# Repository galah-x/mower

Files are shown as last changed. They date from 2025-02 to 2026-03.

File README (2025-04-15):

Repository for files to upgrade a Ryobi RM480e ride on battery mower
from its original 4 75AH lead acid batteries
to Lithium Iron Phosphate (LFP) 100AH batteries
With a battery balance facility.

The 12V LFP batteries have internal battery balance, to balance the 4 cells each contains.
This repo is about balancing the 4 12V batteries to each other.

Discussion at https://hackaday.io/project/202788-ryobi-480e-mower-lfp-battery-upgrade-with-balance

Repo signifiant contents:

VMON is the per battery voltage monitor and balance board
vmon/vmn/vmn.ino    arduino code for an esp32
vmon/vmon/vmon.pdf  board schematic
vmon/vmon/gerbers/  board manufacturing info
vmon/vmon           kicad layout directory

IMON is the current monitor from a current shunt
imon/imon.ino       arduino code for an esp32
vmon/imon/imon.pdf  schematic
there is no imon layout, its hacked onto a vmon board as I discovered a design oversight in the
adc on the mco board near the runup phase. Too much of a hurry to mow the lawn to wait for a pcb to be made and shipped.

MCO is the Mower comms controller board. This is where the mower logic runs.
mcomms/mco/mco.ino     and other files in that directory is the arduino source for the mco board
mcomms/mcomms.pdf      board schematic
mcomms/mcomms          kicad layout files
mcomms/mcomms/gerbers  pcb manufacturing files

MMC is the mower charge controller. Really its a display board next to the power supply with a LCD and
rotary encoder. It displays each battery voltage and balance state, charger voltage, charge current, charge state, mower temperature.
mcharger_if/mcharge_if.pdf       schematic
mcharger_if/mcc/mcc.ino          arduino code, together with remainder of the directory
mcharger_if/mcharger_if/         kicad layout dir
mcharger_if/mcharger_if/gerbers  pcb manufacturing information

PSU is a wifi to serial converter used to allow mco to control and monitor the replacement charger, made from a 1200W 60V smps module and a DPM8624 remote programmable power supply.
vichyctl/psu/psu.ino        arduino code for psu
vichyctl/vichyctl.pdf       schematic for board
vichyctl/vichyctl/gerbers/  layout files
vichyctl/vichyctl           kicad layout directory.   Originally a board to permit remote Wifi access to a vichy VC8145 multimeter 

I didn't draw a charger schematic.
Connect the mains to the smps power supply.
Connect the 60V out of the SMPS to the input pins of the DPM8624
Connect the 4 pins on the PSU board (5V, 0V, TX, RX) to the matching 4 control pins on the DPM86224.
Connect the 2 output pins on the DPM8624 to a charger cable likely repurposed from your old charger
in the charger plug, add a wire to connect the middle sense pin to +48V, ie charger positive. 

mower_system_connect is a top level schematic of new stuff in the mower.
mower_system_connect/mower_system_connect.pdf

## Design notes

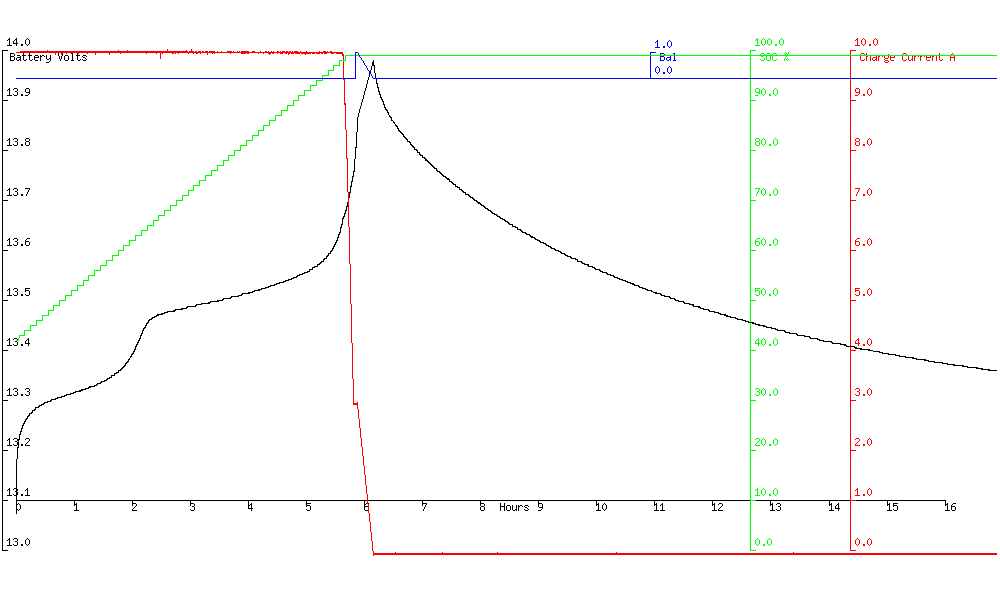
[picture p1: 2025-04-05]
graphs/run2_v.png

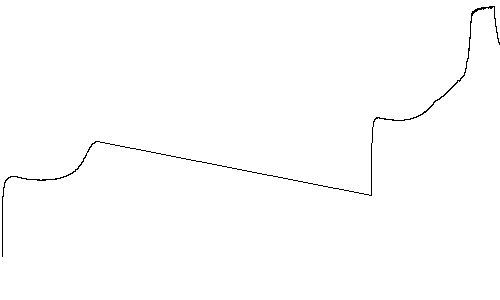
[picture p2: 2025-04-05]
graphs/run1_v.png

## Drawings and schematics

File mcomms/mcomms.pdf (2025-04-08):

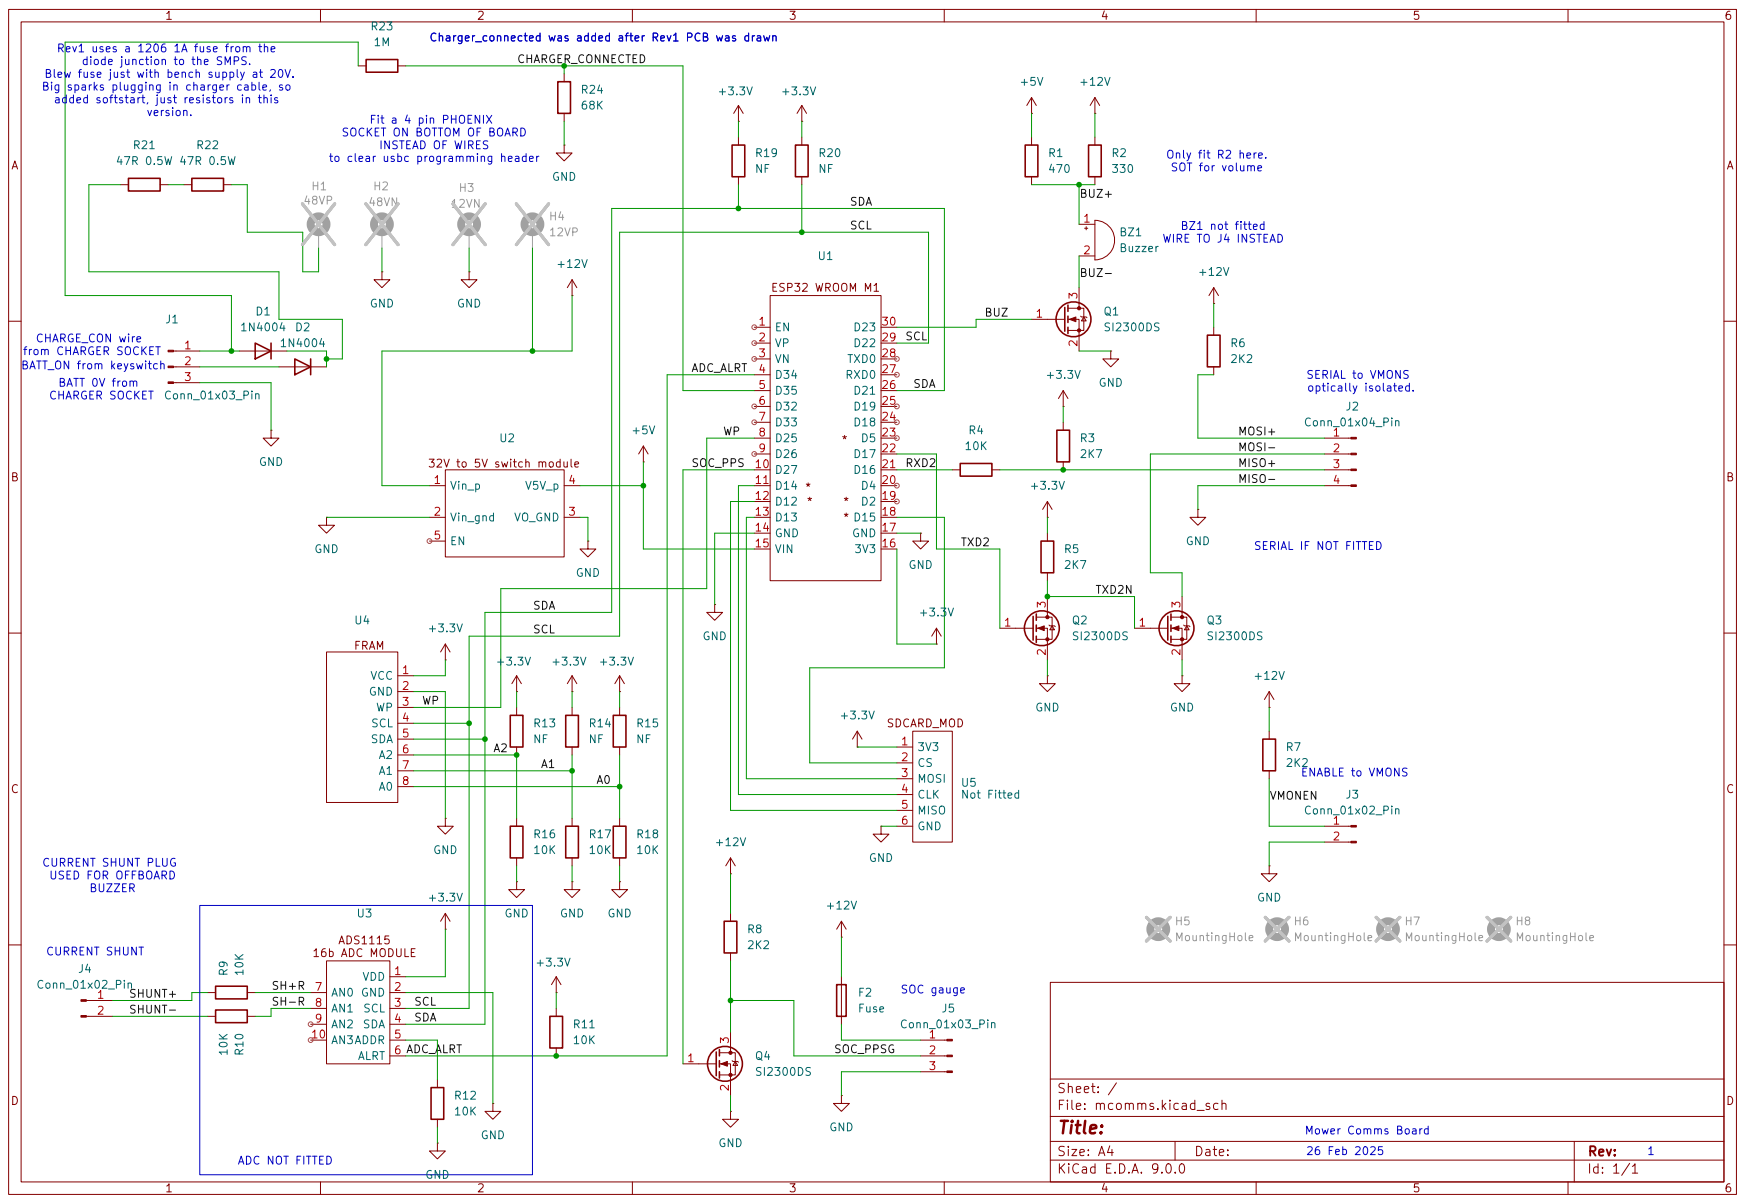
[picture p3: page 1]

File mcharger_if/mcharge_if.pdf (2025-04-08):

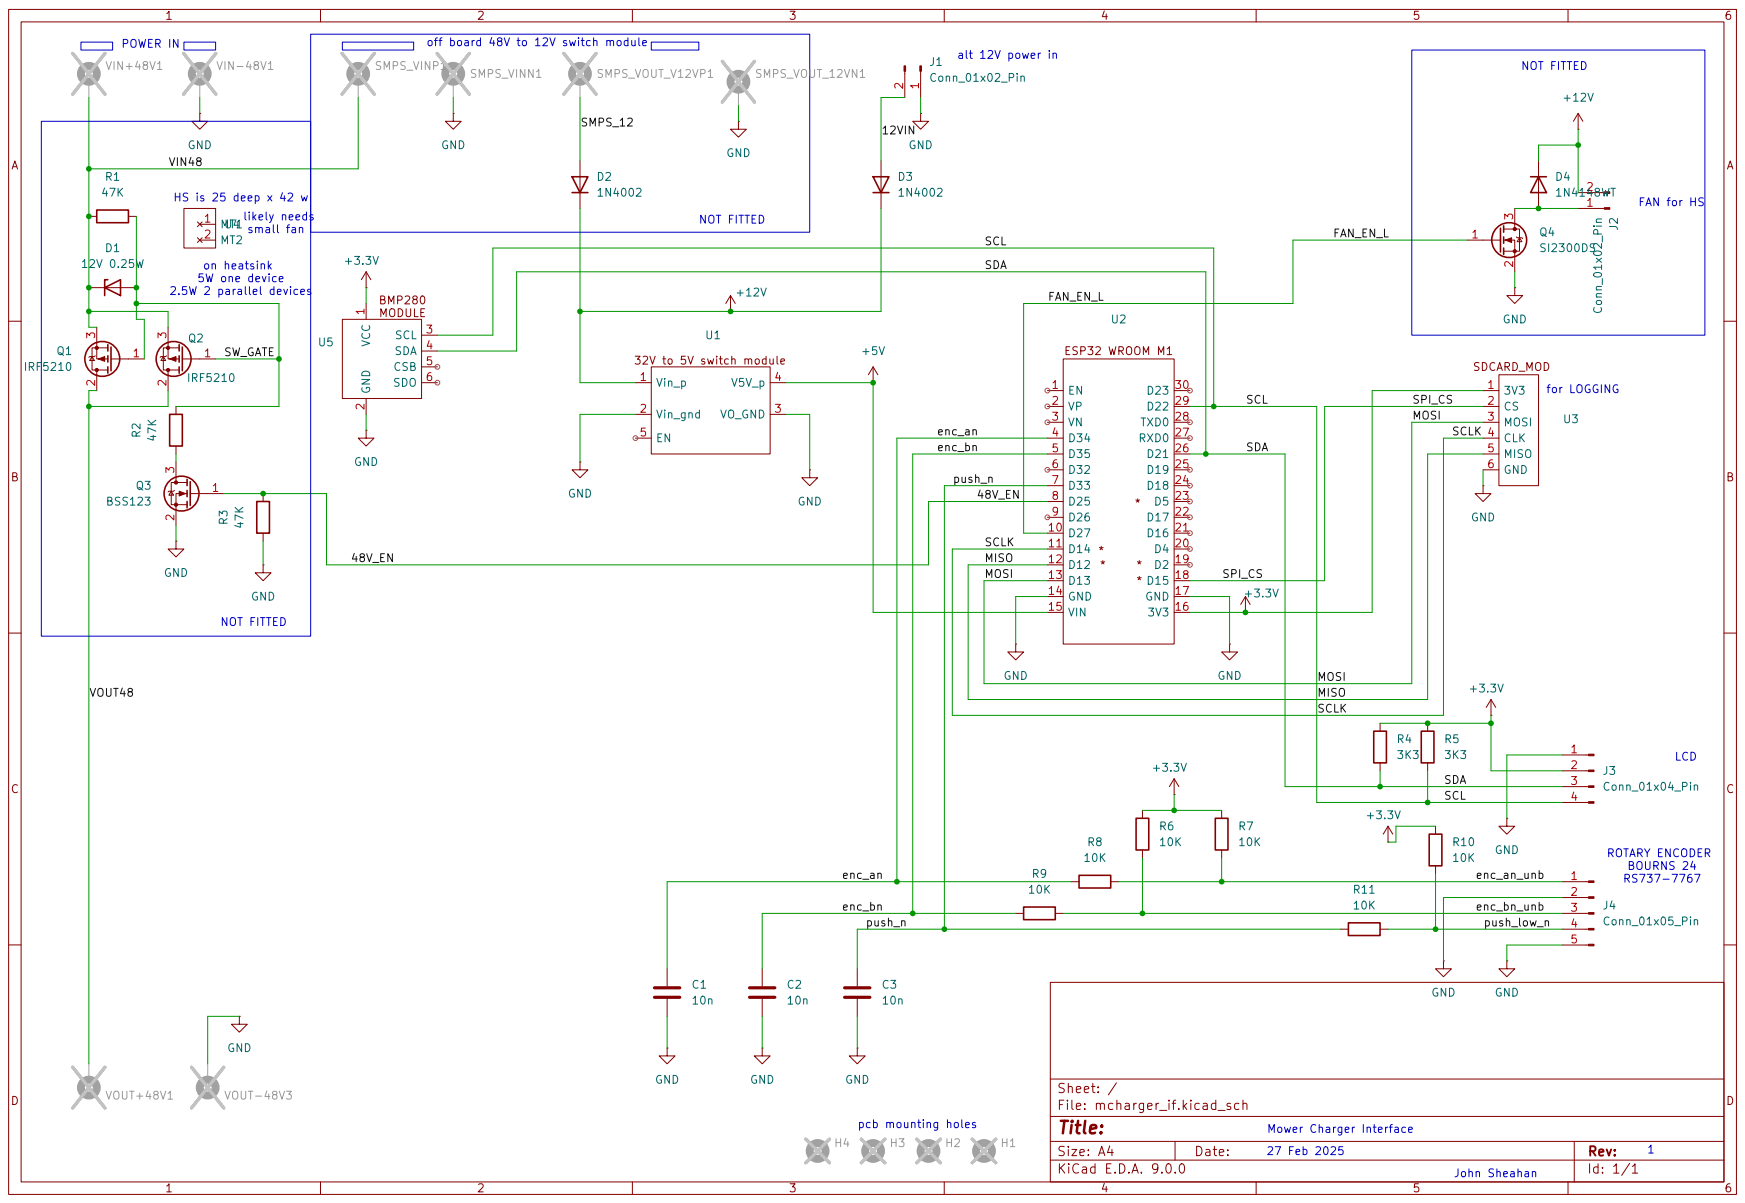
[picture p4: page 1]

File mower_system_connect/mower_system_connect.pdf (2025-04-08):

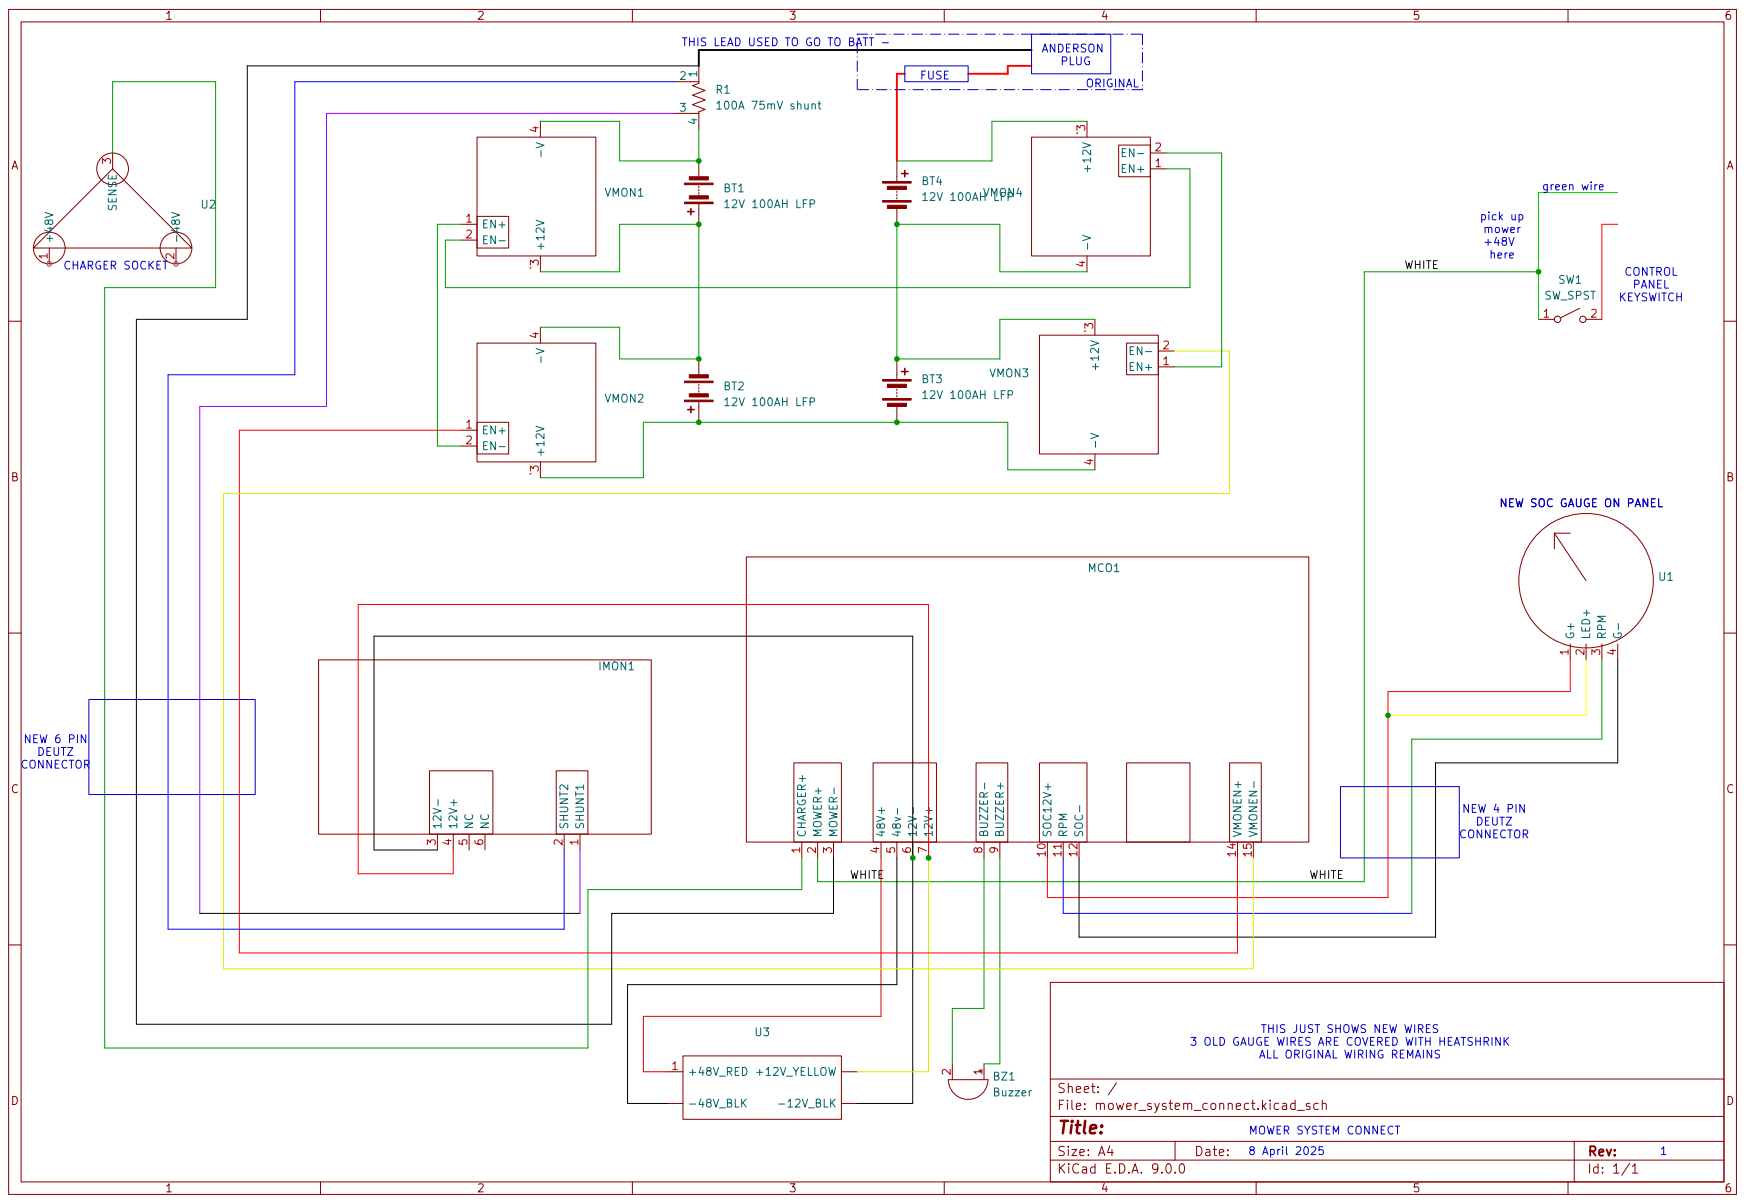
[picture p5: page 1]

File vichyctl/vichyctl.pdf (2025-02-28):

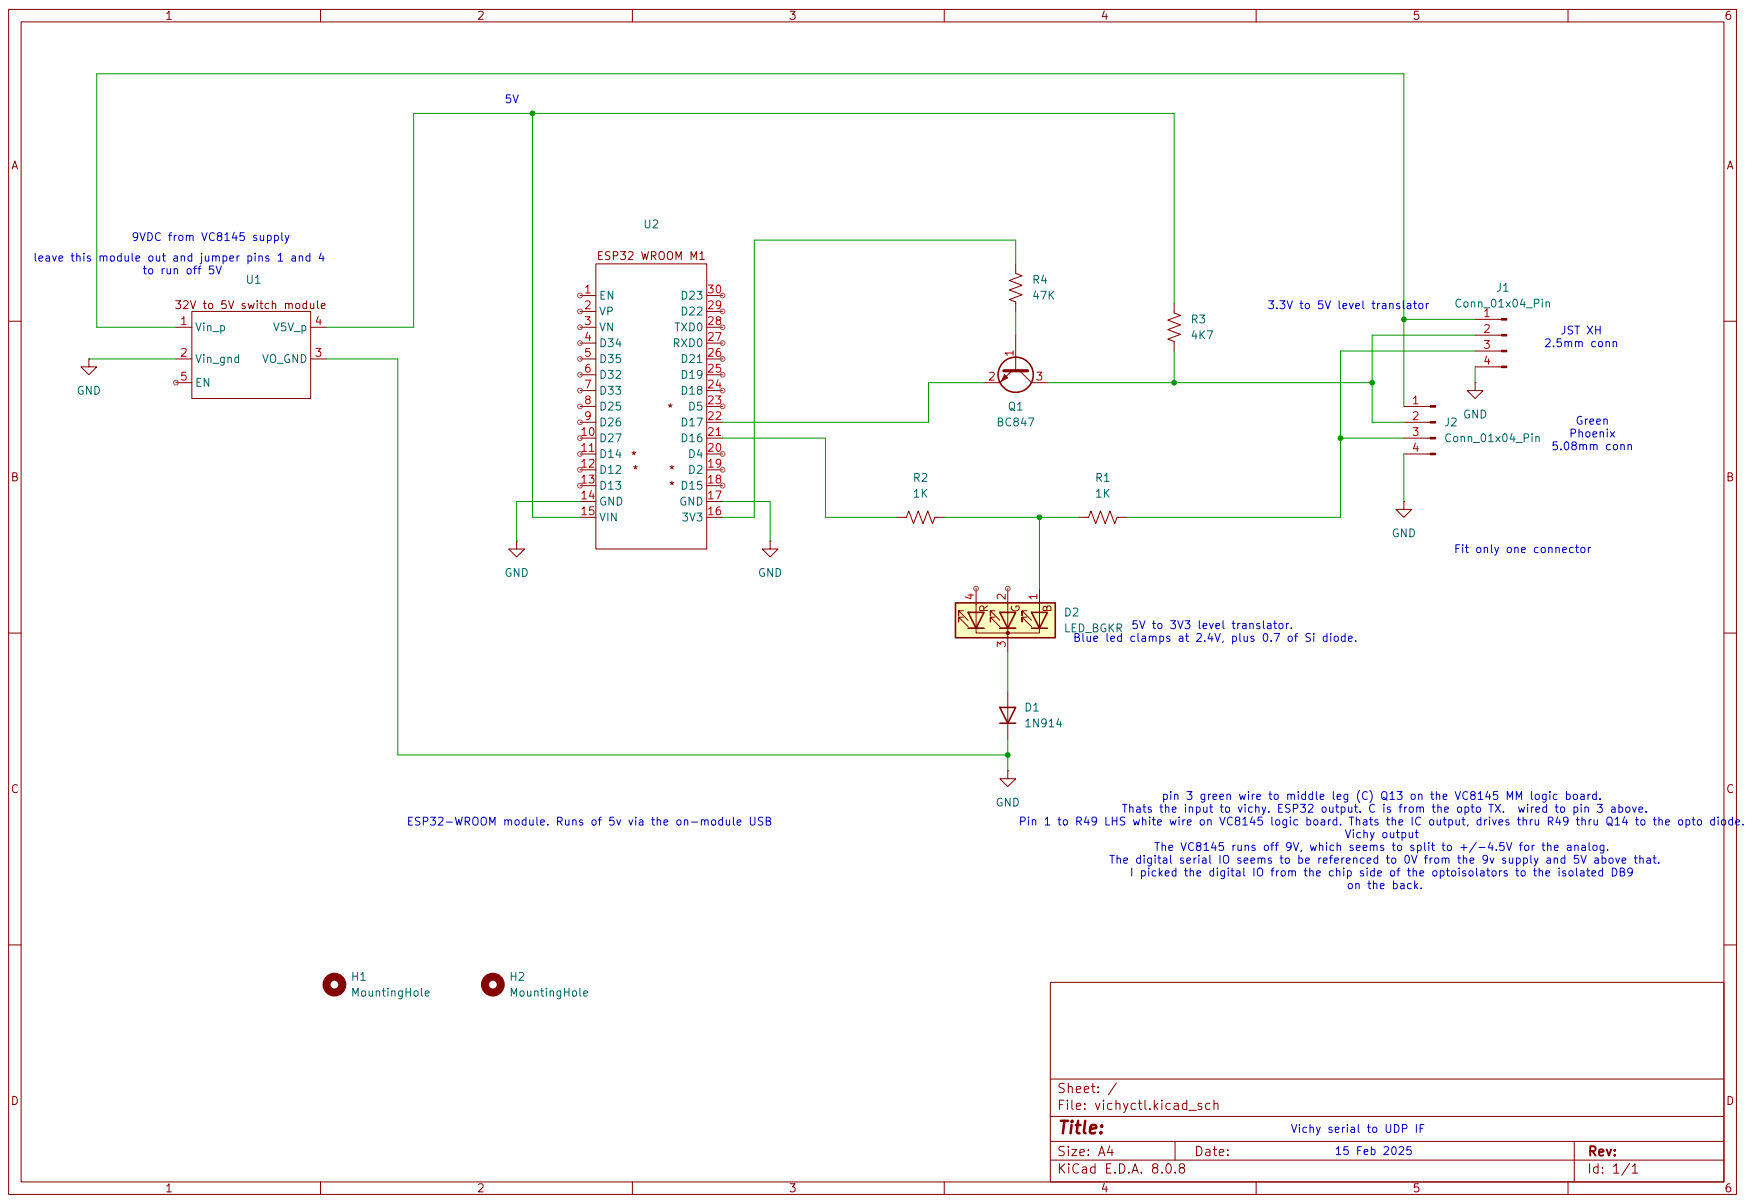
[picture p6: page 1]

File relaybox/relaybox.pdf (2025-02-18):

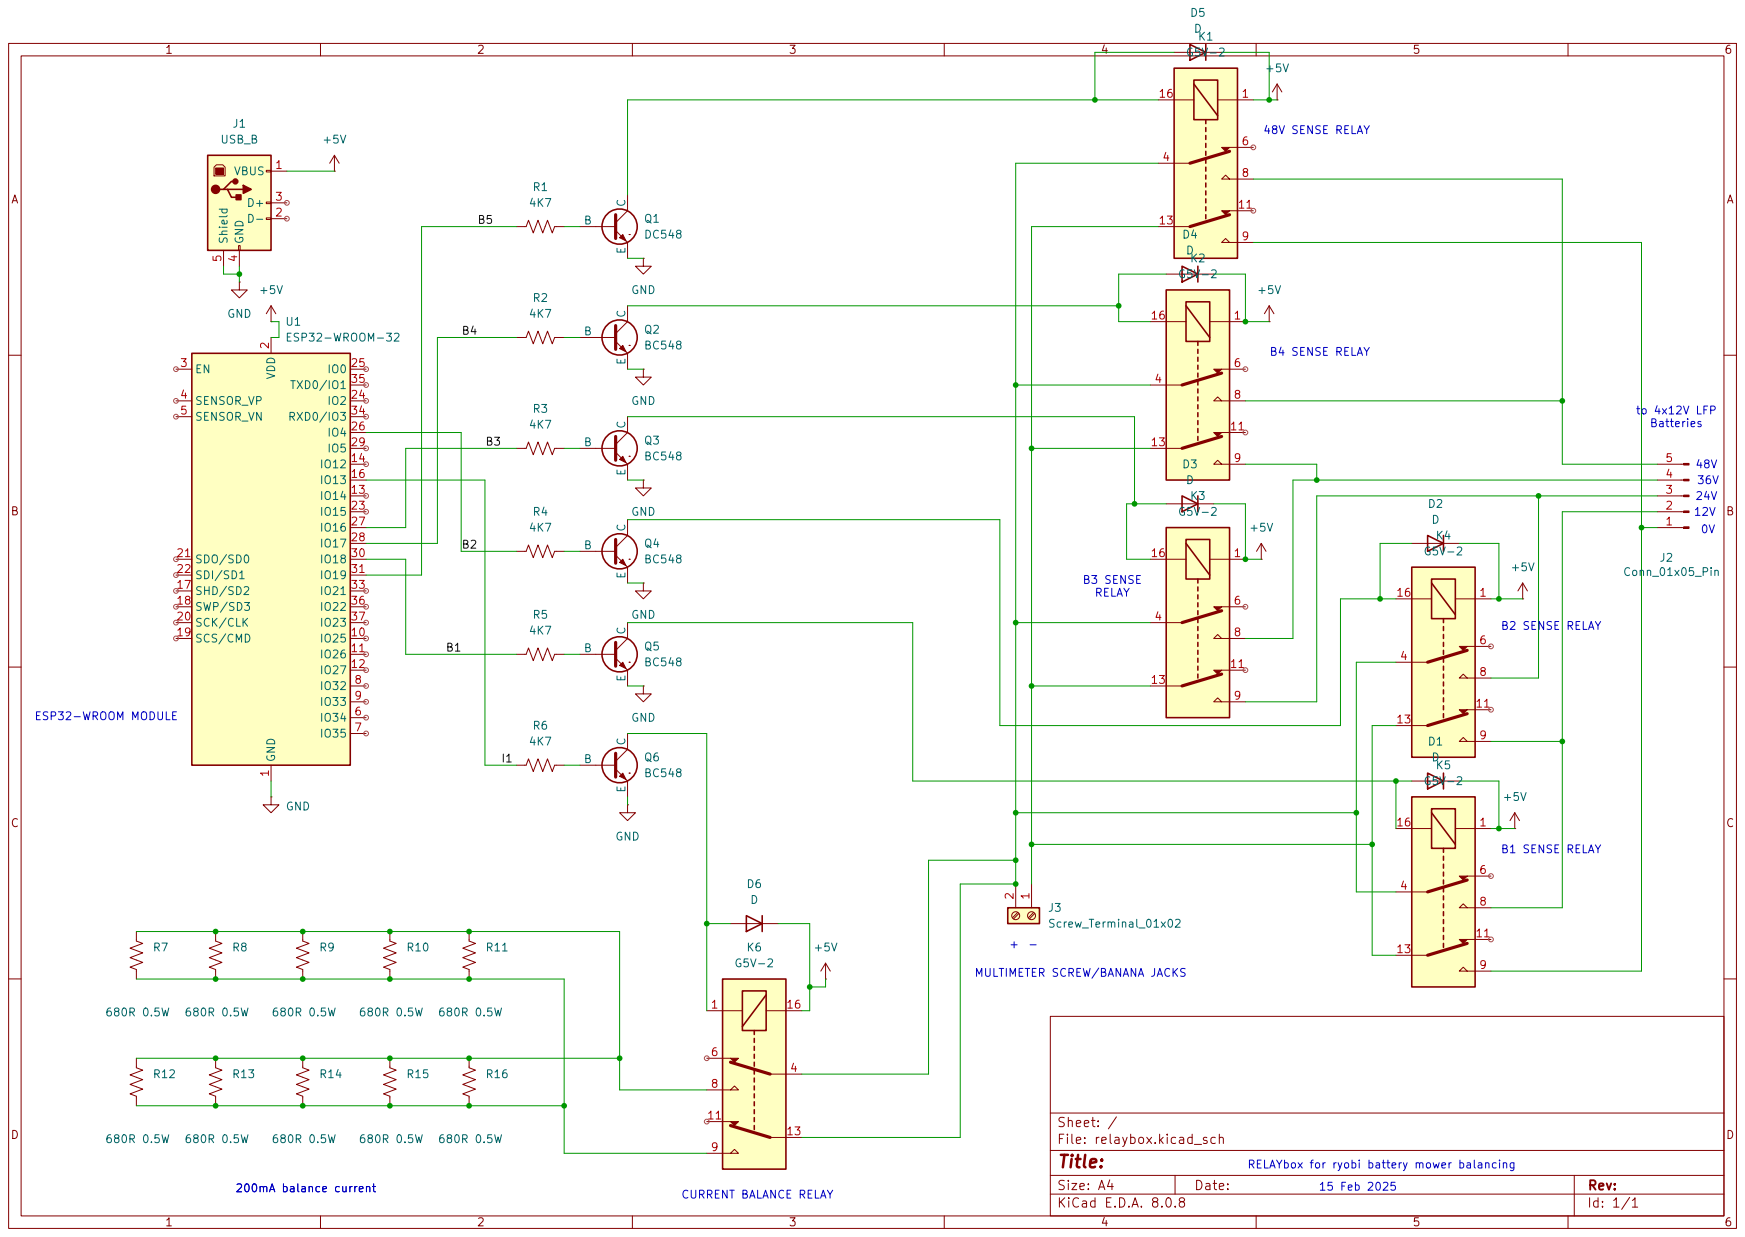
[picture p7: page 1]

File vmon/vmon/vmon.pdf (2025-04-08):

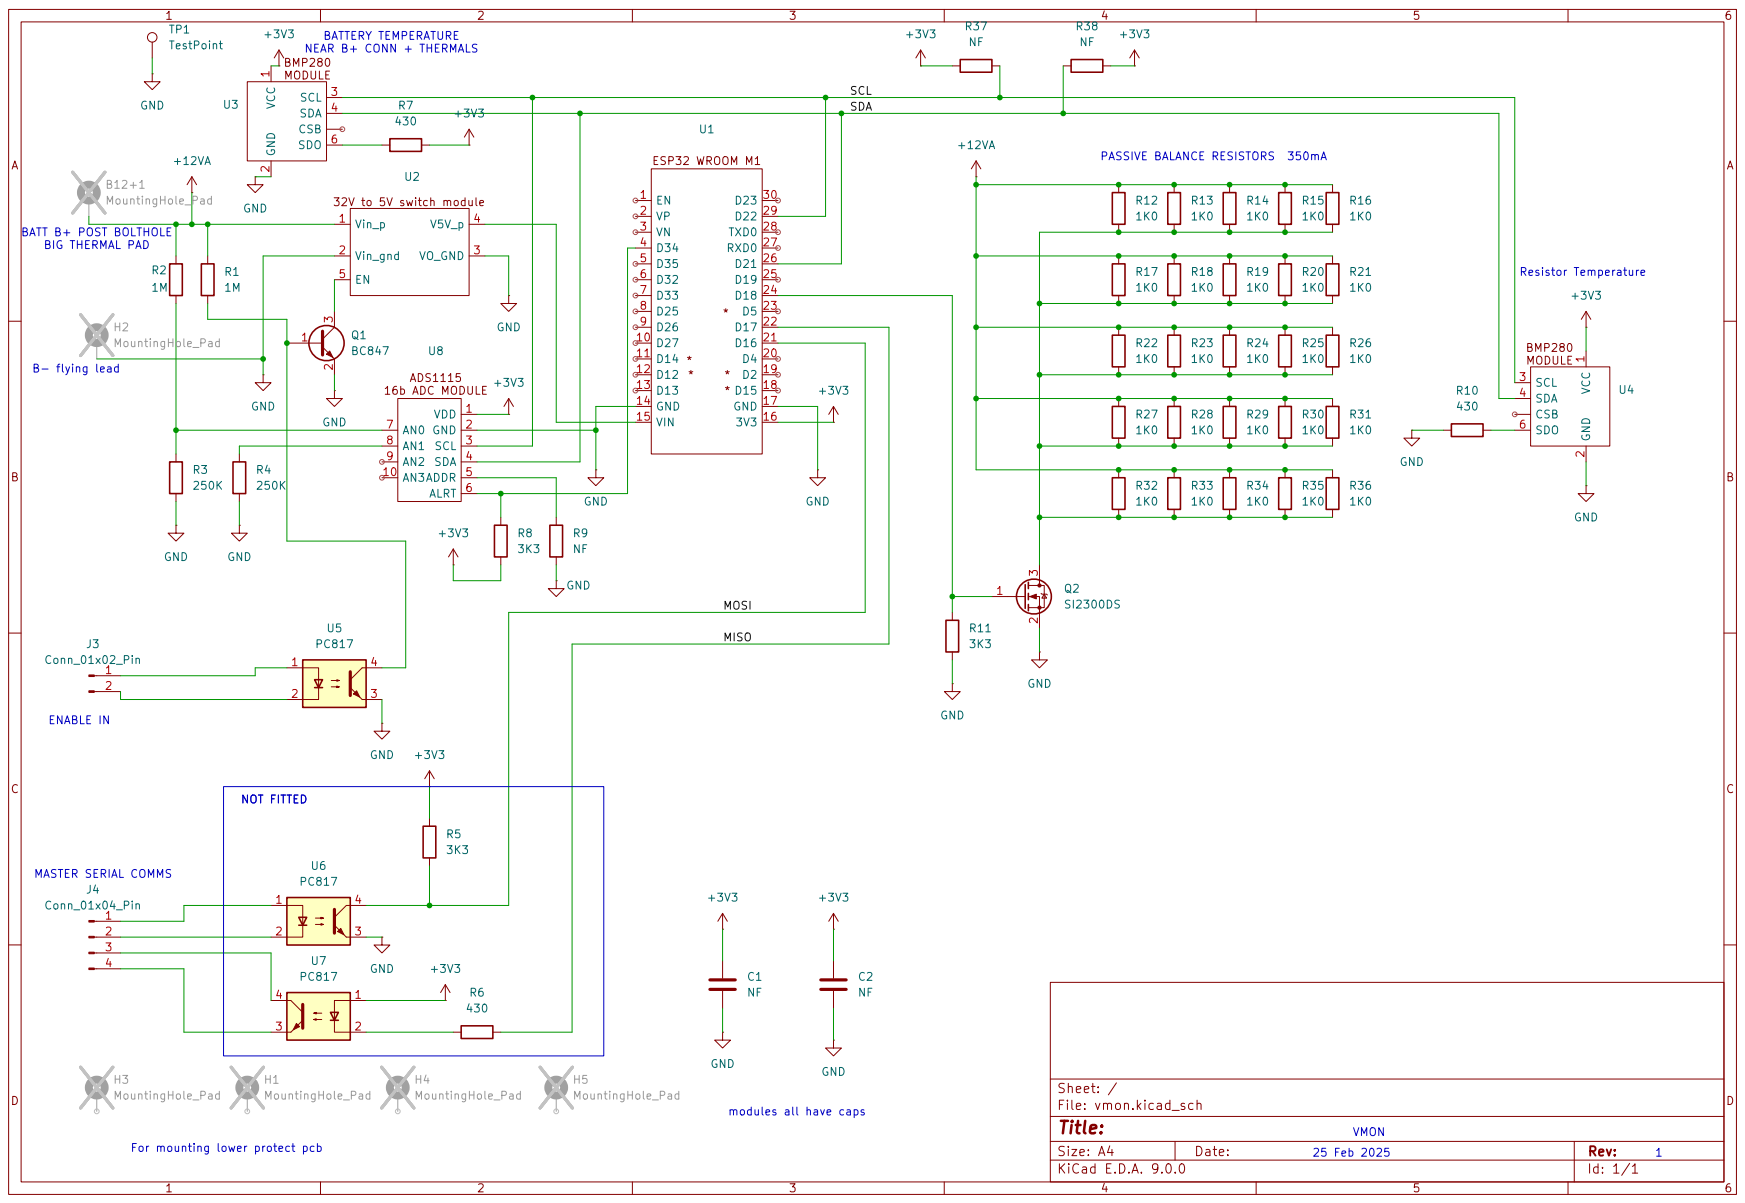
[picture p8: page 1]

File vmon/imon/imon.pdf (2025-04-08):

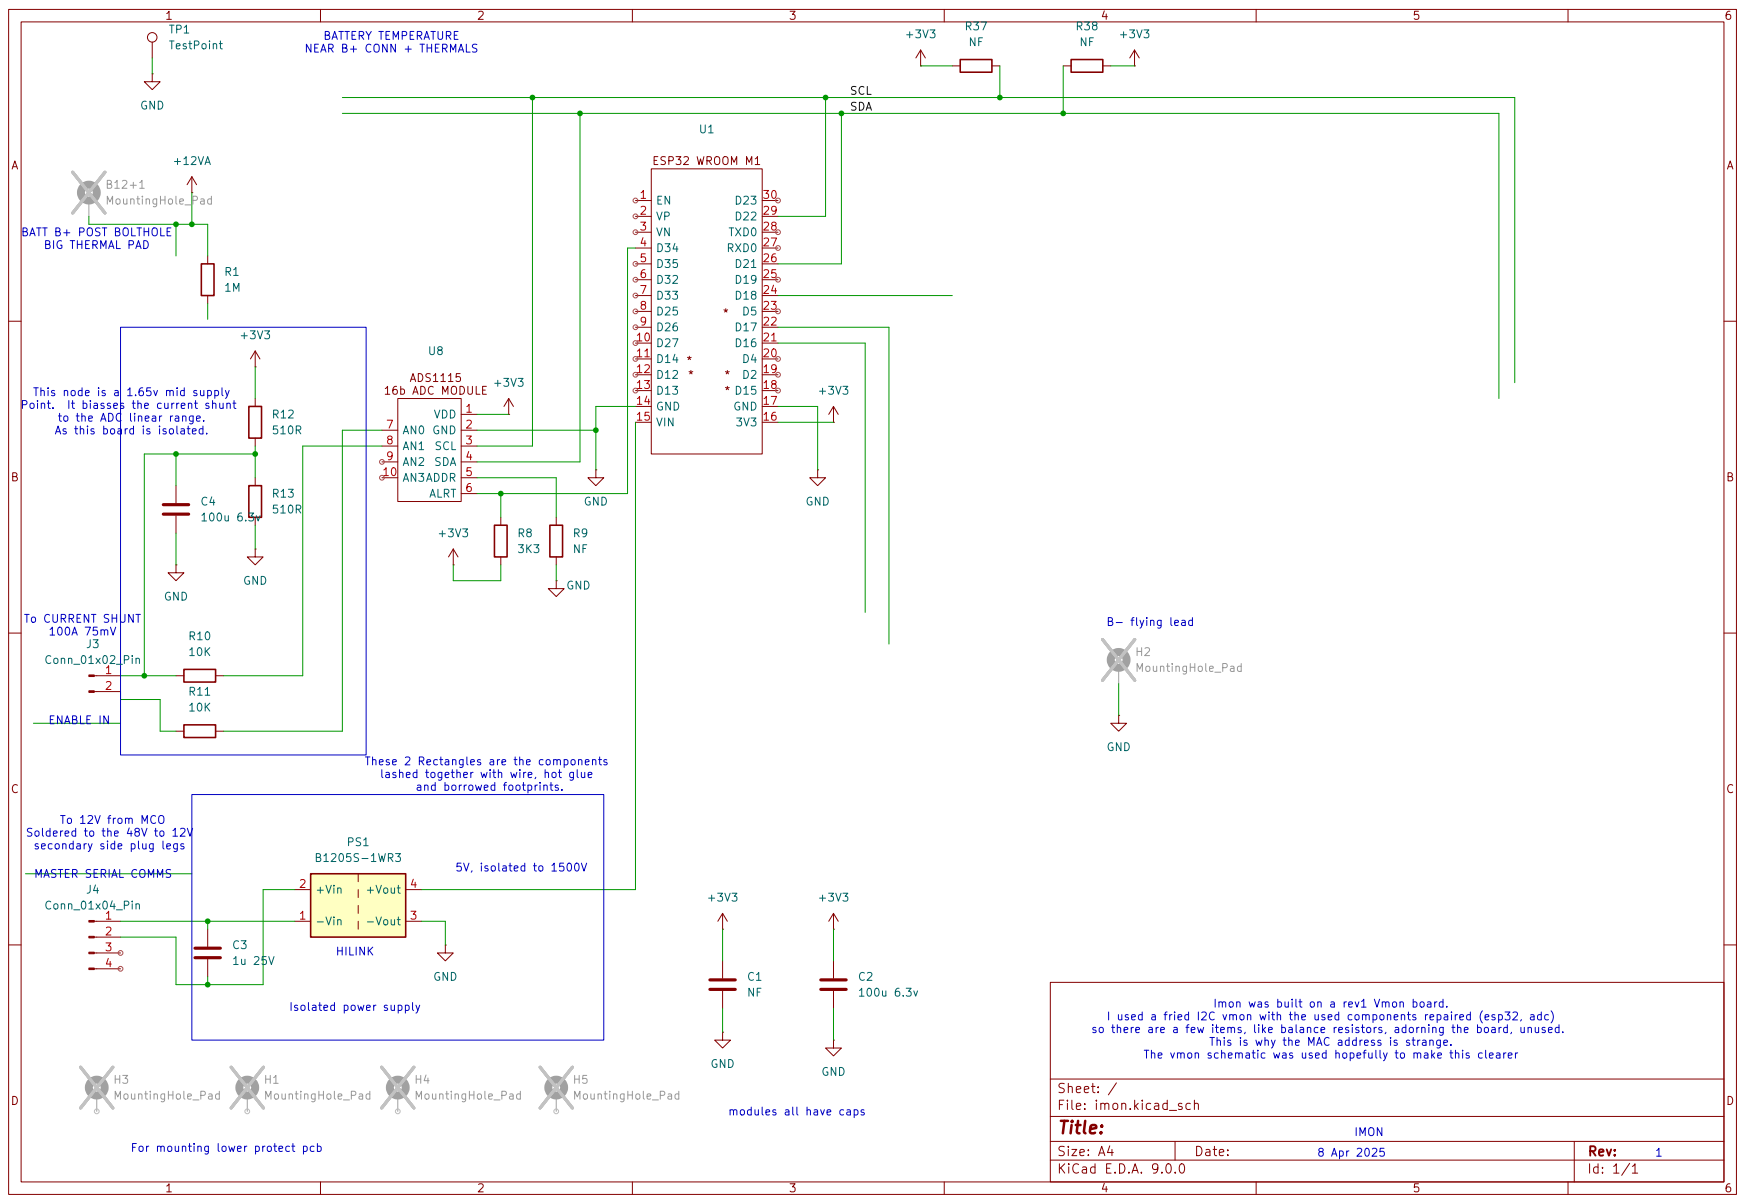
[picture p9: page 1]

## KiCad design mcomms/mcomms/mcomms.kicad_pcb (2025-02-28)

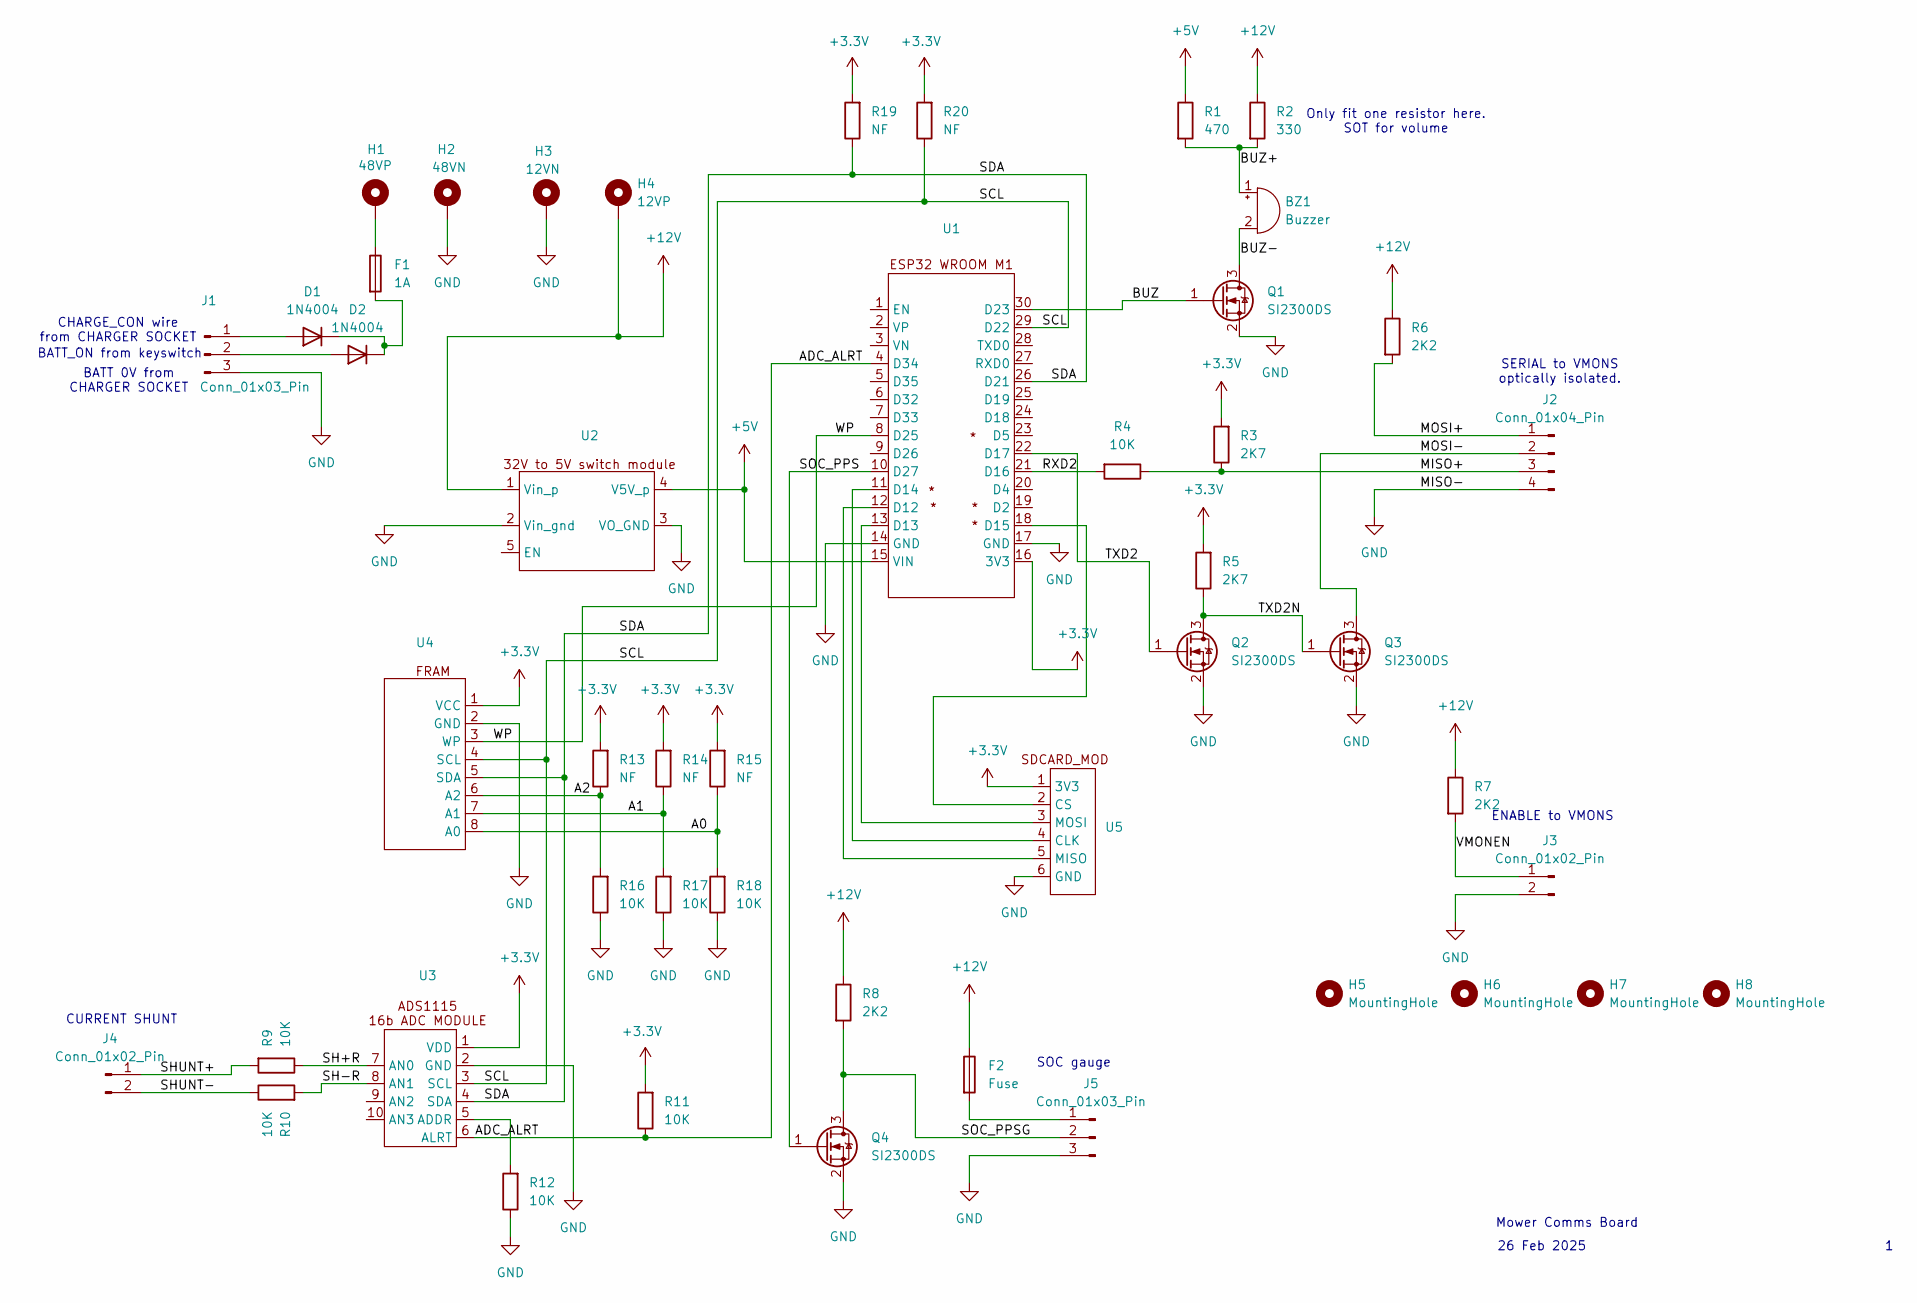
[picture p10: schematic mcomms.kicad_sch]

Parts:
BZ1: Buzzer; Buzzer_12x9.5RM7.6
D1, D2: 1N4004; D_A-405_P12.70mm_Horizontal
F1: 1A; Fuse_1206_3216Metric_Pad1.42x1.75mm_HandSolder
F2: Fuse; Fuse_1206_3216Metric_Pad1.42x1.75mm_HandSolder
H1: 48VP; MountingHole_2.2mm_M2_DIN965_Pad_TopBottom
H2: 48VN; MountingHole_2.2mm_M2_DIN965_Pad_TopBottom
H3: 12VN; MountingHole_2.2mm_M2_DIN965_Pad_TopBottom
H4: 12VP; MountingHole_2.2mm_M2_DIN965_Pad_TopBottom
H5, H6, H7, H8: MountingHole; MountingHole_3.2mm_M3_DIN965_Pad
J1, J5: Conn_01x03_Pin; PhoenixContact_MC_1,5_3-G-5.08_1x03_P5.08mm_Horizontal
J2: Conn_01x04_Pin; PhoenixContact_MC_1,5_4-G-5.08_1x04_P5.08mm_Horizontal
J3, J4: Conn_01x02_Pin; PhoenixContact_MC_1,5_2-G-5.08_1x02_P5.08mm_Horizontal
Q1, Q2, Q3, Q4: SI2300DS; SOT-23
R1: 470; R_Axial_DIN0309_L9.0mm_D3.2mm_P12.70mm_Horizontal
R2: 330; R_Axial_DIN0309_L9.0mm_D3.2mm_P12.70mm_Horizontal
R3, R5: 2K7; R_0805_2012Metric_Pad1.20x1.40mm_HandSolder
R4, R9, R10, R11, R12, R16, R17, R18: 10K; R_0805_2012Metric_Pad1.20x1.40mm_HandSolder
R6, R7, R8: 2K2; R_0805_2012Metric_Pad1.20x1.40mm_HandSolder
R13, R14, R15, R19, R20: NF; R_0805_2012Metric_Pad1.20x1.40mm_HandSolder
U1: ESP32_WROOM_M1
U2: switcher_en
U3: R_Array_SIP10
U4: SIP-8_19x3mm_P2.54mm
U5: R_Array_SIP6

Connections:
+3.3V: R3.2, R5.2, R11.2, R13.2, R14.2, R15.2, R19.2, R20.2, U1.16 (3V3), U3.1 (VDD), U4.1 (VCC), U5.1 (3V3)
+5V: R1.1, U1.15 (VIN), U2.4 (V5V_p)
+12V: F2.1, H4.1, R2.1, R6.1, R7.1, R8.1, U2.1 (Vin_p)
/A0: R15.1, R18.2, U4.8 (A0)
/A1: R14.1, R17.2, U4.7 (A1)
/A2: R13.1, R16.2, U4.6 (A2)
/ADC_ALRT: R11.1, U1.4 (D34), U3.6 (ALRT)
/BUZ: Q1.1 (G), U1.30 (D23)
/BUZ+: BZ1.1 (+), R1.2, R2.2
/BUZ-: BZ1.2 (-), Q1.3 (D)
/MISO+: J2.3, R3.1, R4.1
/MOSI+: J2.1, R6.2
/MOSI-: J2.2, Q3.3 (D)
/RXD2: R4.2, U1.21 (D16)
/SCL: R20.1, U1.29 (D22), U3.3 (SCL), U4.4 (SCL)
/SDA: R19.1, U1.26 (D21), U3.4 (SDA), U4.5 (SDA)
/SH+R: R9.1, U3.7 (AN0)
/SH-R: R10.2, U3.8 (AN1)
/SHUNT+: J4.1, R9.2
/SHUNT-: J4.2, R10.1
/SOC_PPS: Q4.1 (G), U1.10 (D27)
/SOC_PPSG: J5.2, Q4.3 (D), R8.2
/TXD2: Q2.1 (G), U1.22 (D17)
/TXD2N: Q2.3 (D), Q3.1 (G), R5.1
/VMONEN: J3.1, R7.2
/WP: U1.8 (D25), U4.3 (WP)
GND: H2.1, H3.1, J1.3, J2.4, J3.2, J5.3, Q1.2 (S), Q2.2 (S), Q3.2 (S), Q4.2 (S), R12.1, R16.1, R17.1, R18.1, U1.14 (GND), U1.17 (GND), U2.2 (Vin_gnd), U2.3 (VO_GND), U3.2 (GND), U4.2 (GND), U5.6 (GND)
unnamed: D1.2 (A), J1.1
unnamed: D1.1 (K), D2.1 (K), F1.2
unnamed: D2.2 (A), J1.2
unnamed: F1.1, H1.1
unnamed: F2.2, J5.1
unnamed: U1.12 (D12), U5.5 (MISO)
unnamed: U1.13 (D13), U5.3 (MOSI)
unnamed: U1.11 (D14), U5.4 (CLK)
unnamed: U1.18 (D15), U5.2 (CS)
unnamed: R12.2, U3.5 (ADDR)

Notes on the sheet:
SERIAL to VMONS optically isolated.
CHARGE_CON wire from CHARGER SOCKET
CURRENT SHUNT
ENABLE to VMONS
BATT_ON from keyswitch
Mower Comms Board
BATT 0V from CHARGER SOCKET
26 Feb 2025
SOC gauge
Only fit one resistor here. SOT for volume

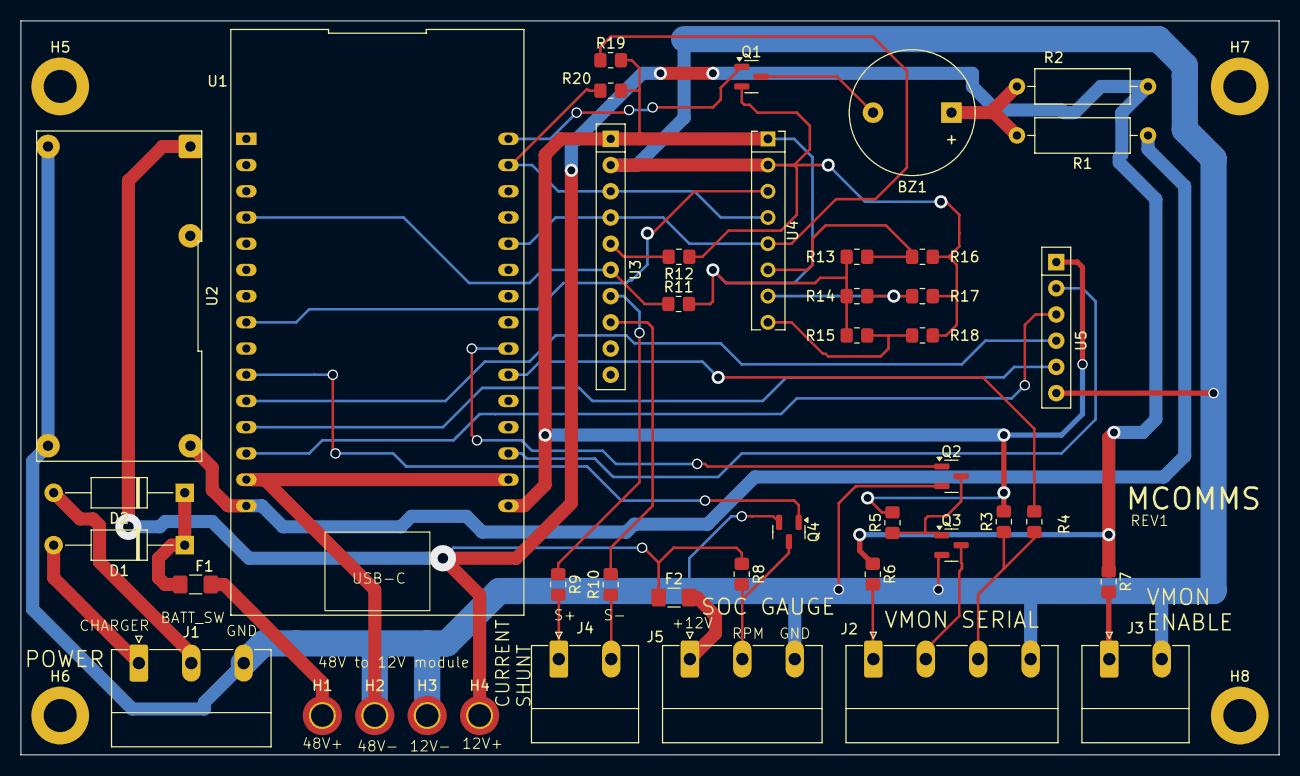
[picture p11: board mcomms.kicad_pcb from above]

Board: 2 copper layers, 121.9 x 71.1 mm, 47 parts (0 on the bottom side), 37 nets.

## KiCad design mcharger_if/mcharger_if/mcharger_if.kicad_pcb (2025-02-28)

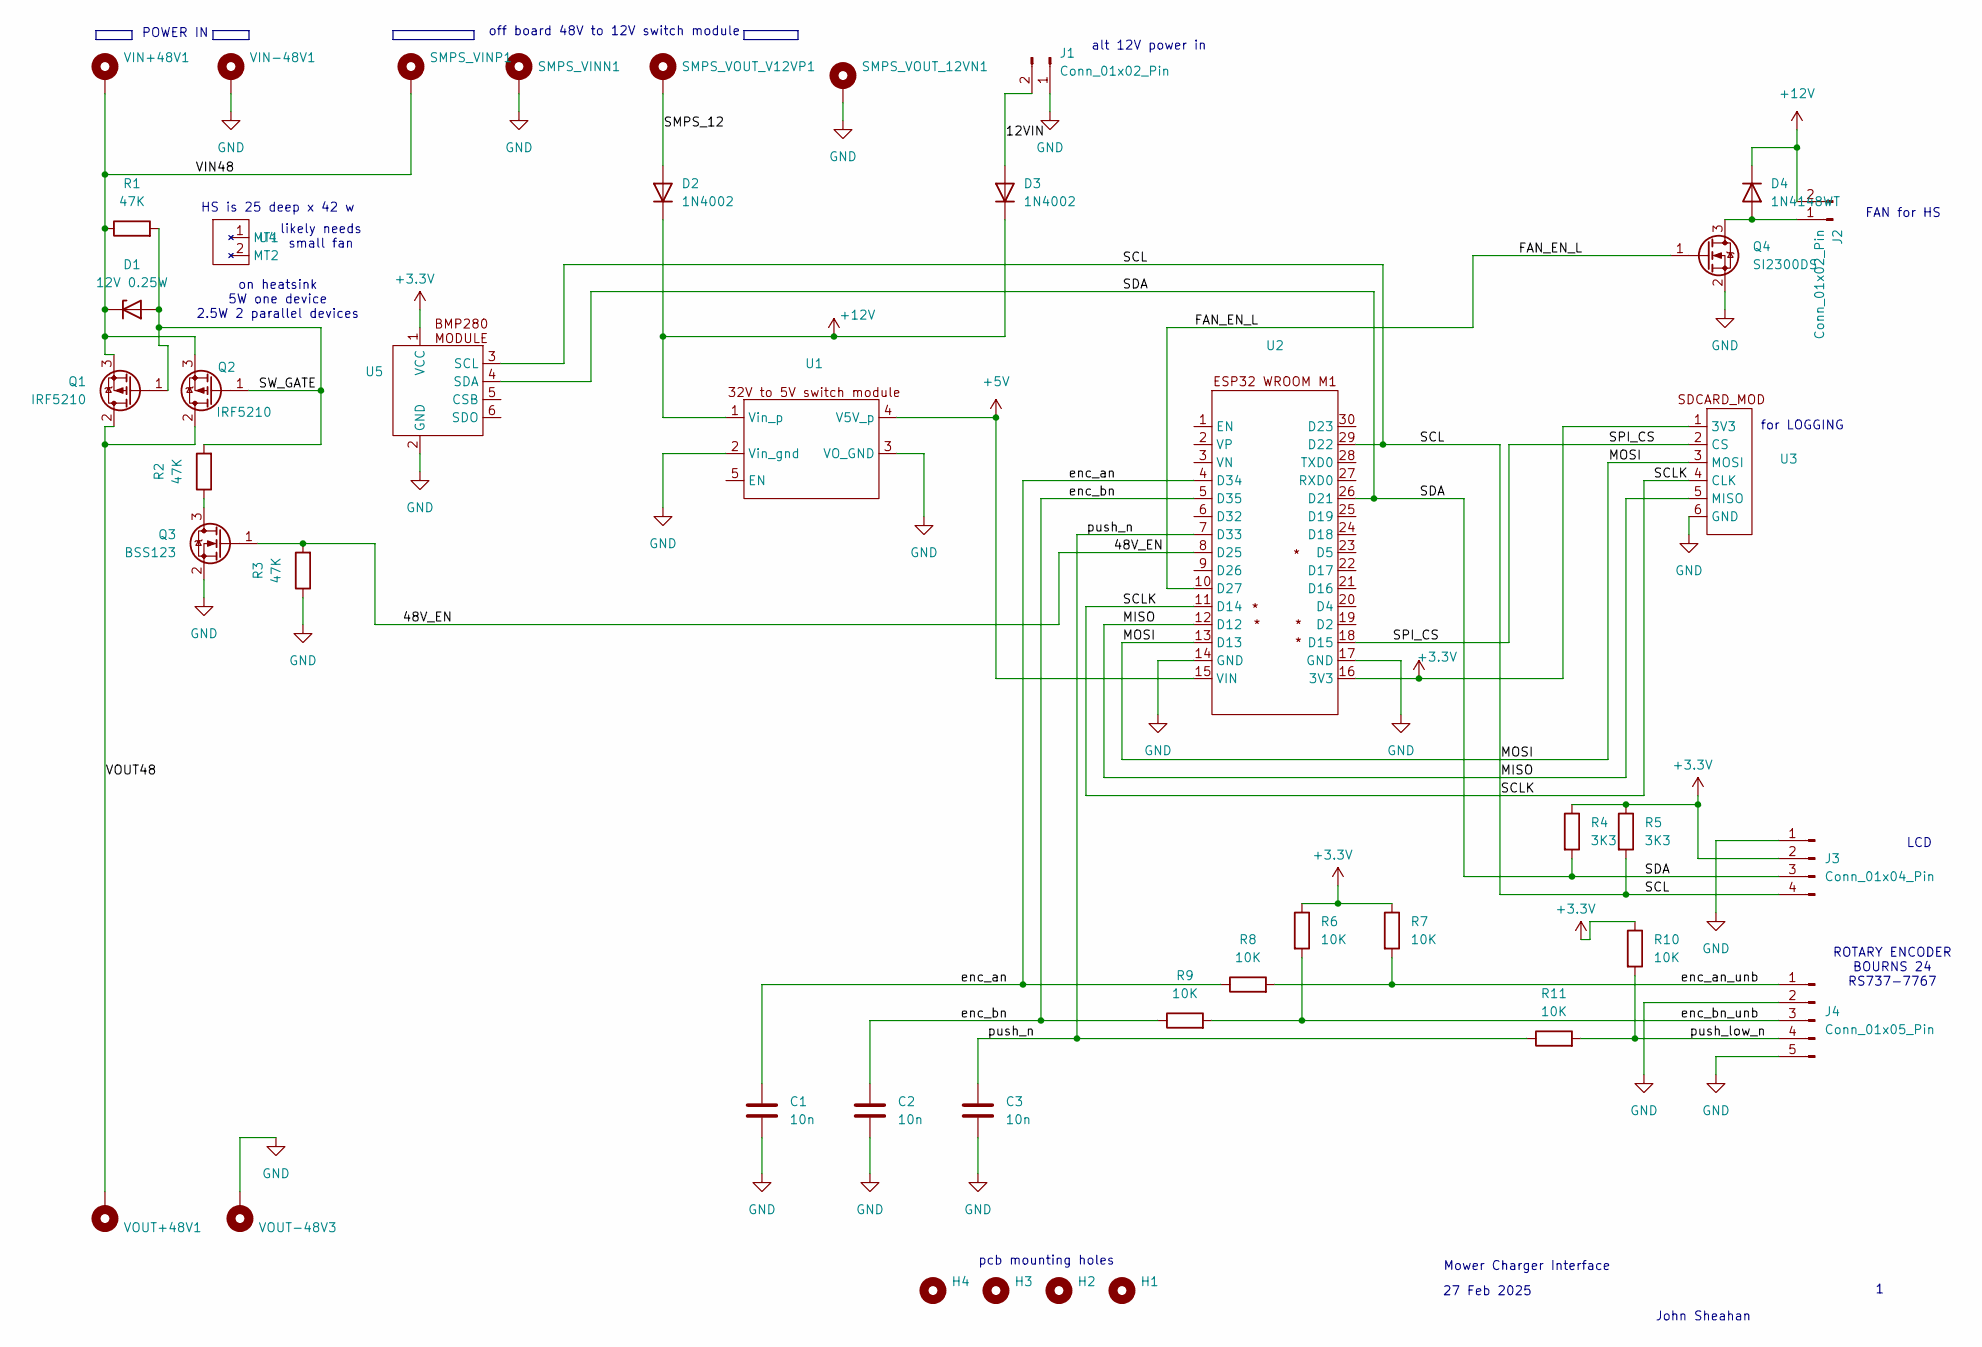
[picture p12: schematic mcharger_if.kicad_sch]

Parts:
C1, C2, C3: 10n; C_0603_1608Metric_Pad1.08x0.95mm_HandSolder
D1: 12V 0.25W; D_0805_2012Metric_Pad1.15x1.40mm_HandSolder
D2, D3: 1N4002; D_DO-41_SOD81_P10.16mm_Horizontal
D4: 1N4148WT; D_SOD-523
H1, H2, H3, H4: MountingHole; MountingHole_3.2mm_M3_DIN965
J1, J2: Conn_01x02_Pin; PhoenixContact_MC_1,5_2-G-5.08_1x02_P5.08mm_Horizontal
J3: Conn_01x04_Pin; JST_XH_B4B-XH-AM_1x04_P2.50mm_Vertical
J4: Conn_01x05_Pin; JST_XH_B5B-XH-A_1x05_P2.50mm_Vertical
Q1, Q2: IRF5210; TO-220-3_Vertical
Q3: BSS123; SOT-23
Q4: SI2300DS; SOT-23
R1, R2, R3: 47K; R_0805_2012Metric_Pad1.20x1.40mm_HandSolder
R4, R5: 3K3; R_0805_2012Metric_Pad1.20x1.40mm_HandSolder
R6, R7, R8, R9, R10, R11: 10K; R_0805_2012Metric_Pad1.20x1.40mm_HandSolder
SMPS_VINN1: MountingHole_Pad; MountingHole_2.2mm_M2_DIN965_Pad_TopBottom
SMPS_VINP1: MountingHole_Pad; MountingHole_2.2mm_M2_DIN965_Pad_TopBottom
SMPS_VOUT_12VN1: MountingHole_Pad; MountingHole_2.2mm_M2_DIN965_Pad_TopBottom
SMPS_VOUT_V12VP1: MountingHole_Pad; MountingHole_2.2mm_M2_DIN965_Pad_TopBottom
U1: switcher_en
U2: ESP32_WROOM_M1
U3, U5: R_Array_SIP6
U4: TO220_m1
VIN+48V1: MountingHole_Pad; MountingHole_3.2mm_M3_DIN965_Pad_TopBottom
VIN-48V1: MountingHole_Pad; MountingHole_3.2mm_M3_DIN965_Pad_TopBottom
VOUT+48V1: MountingHole_Pad; MountingHole_3.2mm_M3_DIN965_Pad_TopBottom
VOUT-48V3: MountingHole_Pad; MountingHole_3.2mm_M3_DIN965_Pad_TopBottom

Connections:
+3.3V: J3.2, R4.1, R5.1, R6.1, R7.1, R10.1, U2.16 (3V3), U3.1 (3V3), U5.1 (VCC)
+5V: U1.4 (V5V_p), U2.15 (VIN)
+12V: D2.1 (K), D3.1 (K), D4.1 (K), J2.2, U1.1 (Vin_p)
/12VIN: D3.2 (A), J1.2
/48V_EN: Q3.1 (G), R3.2, U2.8 (D25)
/FAN_EN_L: Q4.1 (G), U2.10 (D27)
/SDA: J3.3, R4.2, U2.26 (D21), U5.4 (SDA)
/SMPS_12: D2.2 (A), SMPS_VOUT_V12VP1.1
/SPI_CS: U2.18 (D15), U3.2 (CS)
/SW_GATE: D1.2 (A), Q1.1 (G), Q2.1 (G), R1.2, R2.2
/VIN48: D1.1 (K), Q1.3 (S), Q2.3 (S), R1.1, SMPS_VINP1.1, VIN+48V1.1
/VOUT48: Q1.2 (D), Q2.2 (D), VOUT+48V1.1
/enc_an: C1.1, R8.1, U2.4 (D34)
/enc_an_unb: J4.1, R7.2, R8.2
/enc_bn: C2.1, R9.1, U2.5 (D35)
/enc_bn_unb: J4.3, R6.2, R9.2
/push_low_n: J4.4, R10.2, R11.2
/push_n: C3.1, R11.1, U2.7 (D33)
GND: C1.2, C2.2, C3.2, J1.1, J3.1, J4.2, J4.5, Q3.2 (S), Q4.2 (S), R3.1, SMPS_VINN1.1, SMPS_VOUT_12VN1.1, U1.2 (Vin_gnd), U1.3 (VO_GND), U2.14 (GND), U2.17 (GND), U3.6 (GND), U5.2 (GND), VIN-48V1.1, VOUT-48V3.1
unnamed: D4.2 (A), J2.1, Q4.3 (D)
unnamed: Q3.3 (D), R2.1

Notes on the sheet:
likely needs small fan
for LOGGING
POWER IN
FAN for HS
27 Feb 2025
John Sheahan
Mower Charger Interface
HS is 25 deep x 42 w
pcb mounting holes
off board 48V to 12V switch module
LCD
on heatsink 5W one device 2.5W 2 parallel devices
ROTARY ENCODER BOURNS 24 RS737-7767
alt 12V power in

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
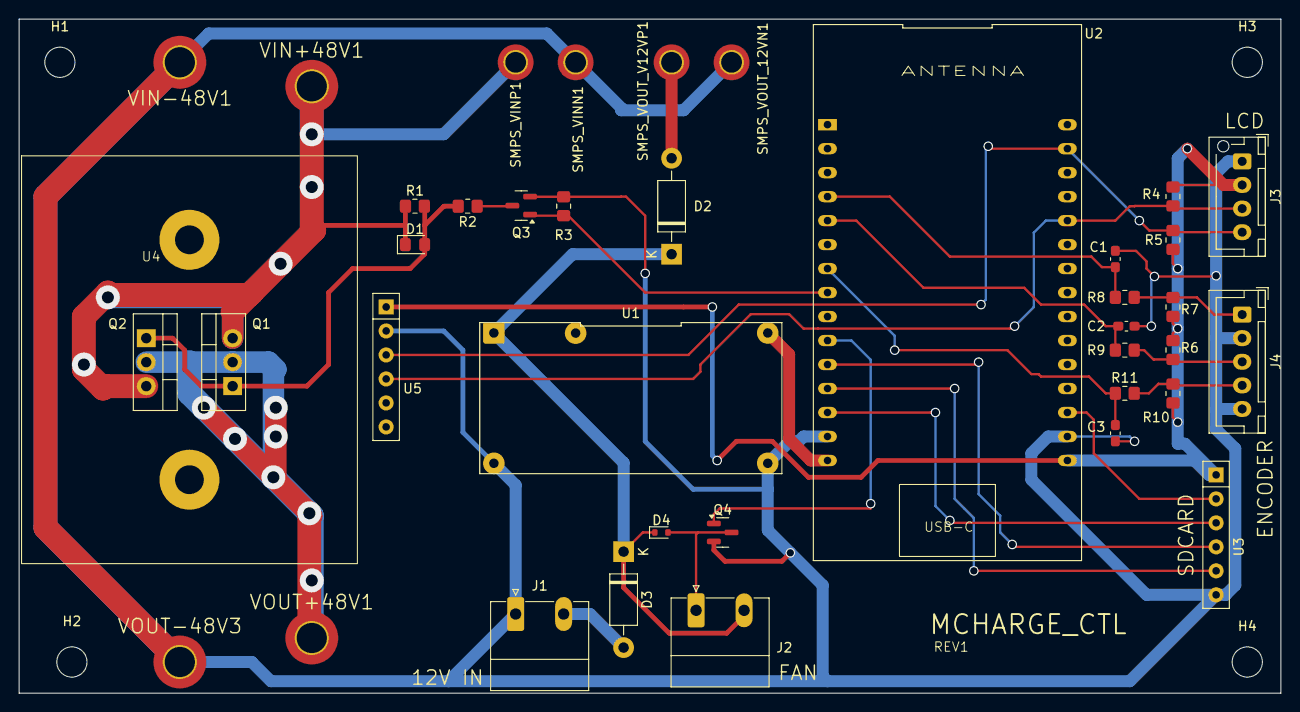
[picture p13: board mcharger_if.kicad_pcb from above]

Board: 2 copper layers, 133.6 x 71.4 mm, 43 parts (0 on the bottom side), 25 nets.

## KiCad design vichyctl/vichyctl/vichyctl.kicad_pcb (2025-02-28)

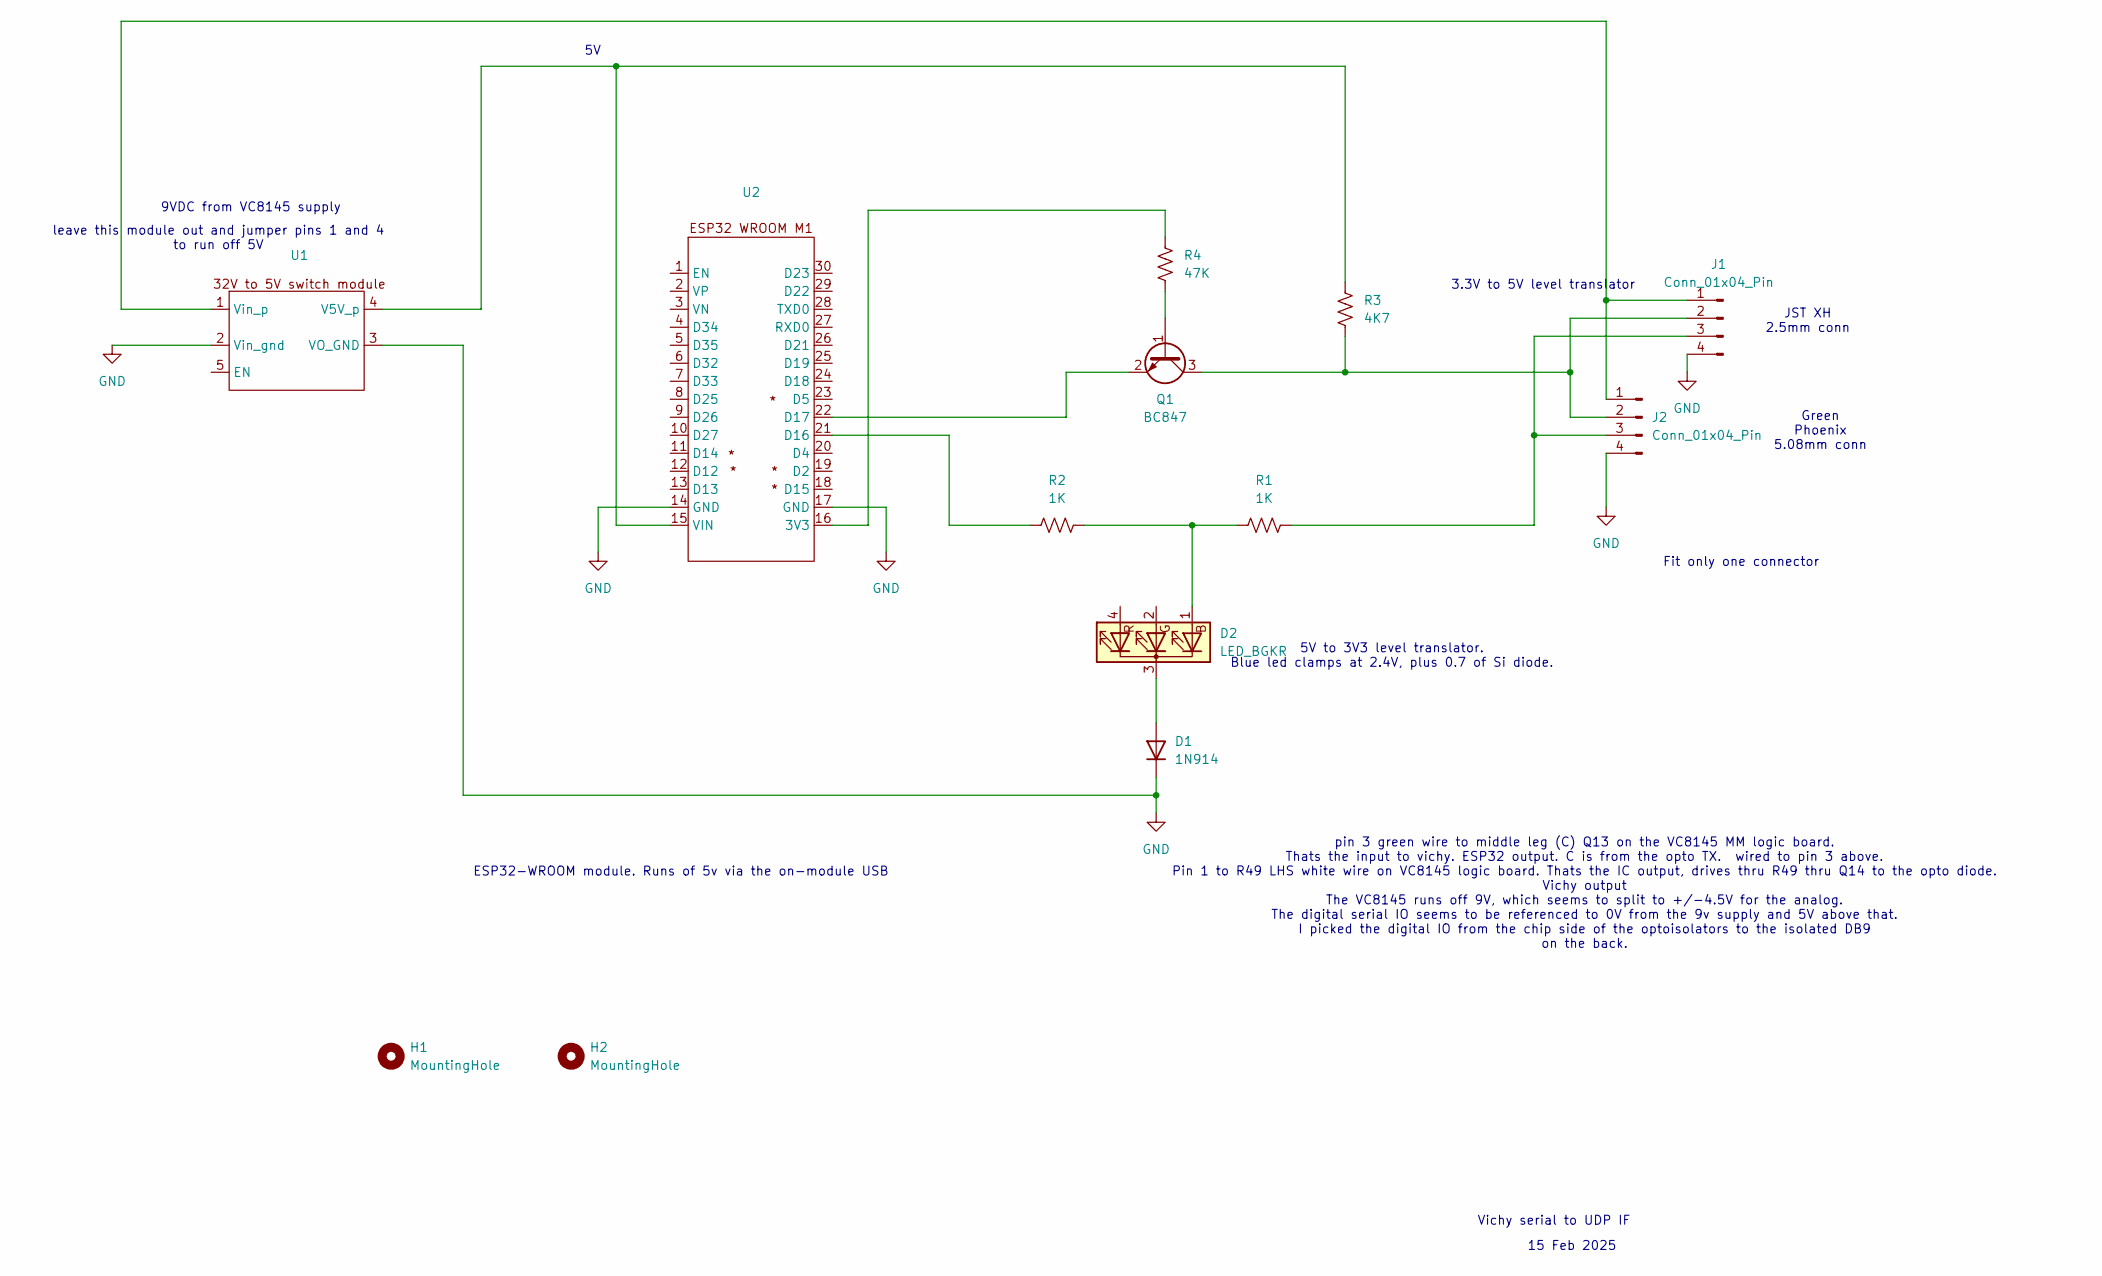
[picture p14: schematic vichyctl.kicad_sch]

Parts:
D1: 1N914; D_0603_1608Metric_Pad1.05x0.95mm_HandSolder
D2: LED_BGKR; LED_D5.0mm-4_RGB_Wide_Pins
H1, H2: MountingHole; MountingHole_3.2mm_M3_ISO7380
J1: Conn_01x04_Pin; JST_XH_B4B-XH-A_1x04_P2.50mm_Vertical
J2: Conn_01x04_Pin; PhoenixContact_MC_1,5_4-G-5.08_1x04_P5.08mm_Horizontal
Q1: BC847; SOT-23
R1, R2: 1K; R_0805_2012Metric_Pad1.20x1.40mm_HandSolder
R3: 4K7; R_0805_2012Metric_Pad1.20x1.40mm_HandSolder
R4: 47K; R_0805_2012Metric_Pad1.20x1.40mm_HandSolder
U1: switcher_en
U2: ESP32_WROOM_M1

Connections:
GND: D1.1 (K), J1.4, J2.4, U1.2 (Vin_gnd), U1.3 (VO_GND), U2.14 (GND), U2.17 (GND)
unnamed: D1.2 (A), D2.3 (K)
unnamed: D2.1 (BA), R1.1, R2.2
unnamed: J1.1, J2.1, U1.1 (Vin_p)
unnamed: J1.2, J2.2, Q1.3 (C), R3.2
unnamed: J1.3, J2.3, R1.2
unnamed: Q1.1 (B), R4.1
unnamed: Q1.2 (E), U2.22 (D17)
unnamed: R4.2, U2.16 (3V3)
unnamed: R2.1, U2.21 (D16)
unnamed: R3.1, U1.4 (V5V_p), U2.15 (VIN)

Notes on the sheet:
Fit only one connector
5V to 3V3 level translator. Blue led clamps at 2.4V, plus 0.7 of Si diode.
ESP32-WROOM module. Runs of 5v via the on-module USB
9VDC from VC8145 supply
leave this module out and jumper pins 1 and 4 to run off 5V
JST XH 2.5mm conn
Green Phoenix 5.08mm conn
15 Feb 2025
3.3V to 5V level translator
pin 3 green wire to middle leg (C) Q13 on the VC8145 MM logic board. Thats the input to vichy. ESP32 output. C is from the opto TX. wired to pin 3 above. Pin 1 to R49 LHS white wire on VC8145 logic board. Thats the IC output, drives thru R49 thru Q14 to the opto diode. Vichy output The VC8145 runs 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
Vichy serial to UDP IF

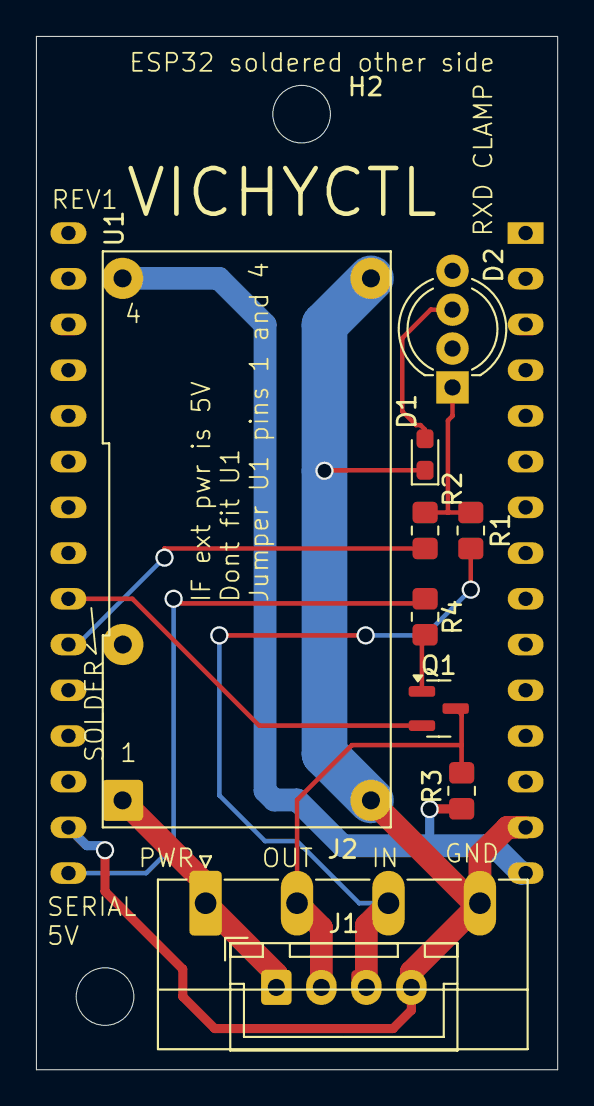
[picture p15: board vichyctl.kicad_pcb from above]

Board: 2 copper layers, 29.0 x 57.4 mm, 13 parts (1 on the bottom side), 11 nets.

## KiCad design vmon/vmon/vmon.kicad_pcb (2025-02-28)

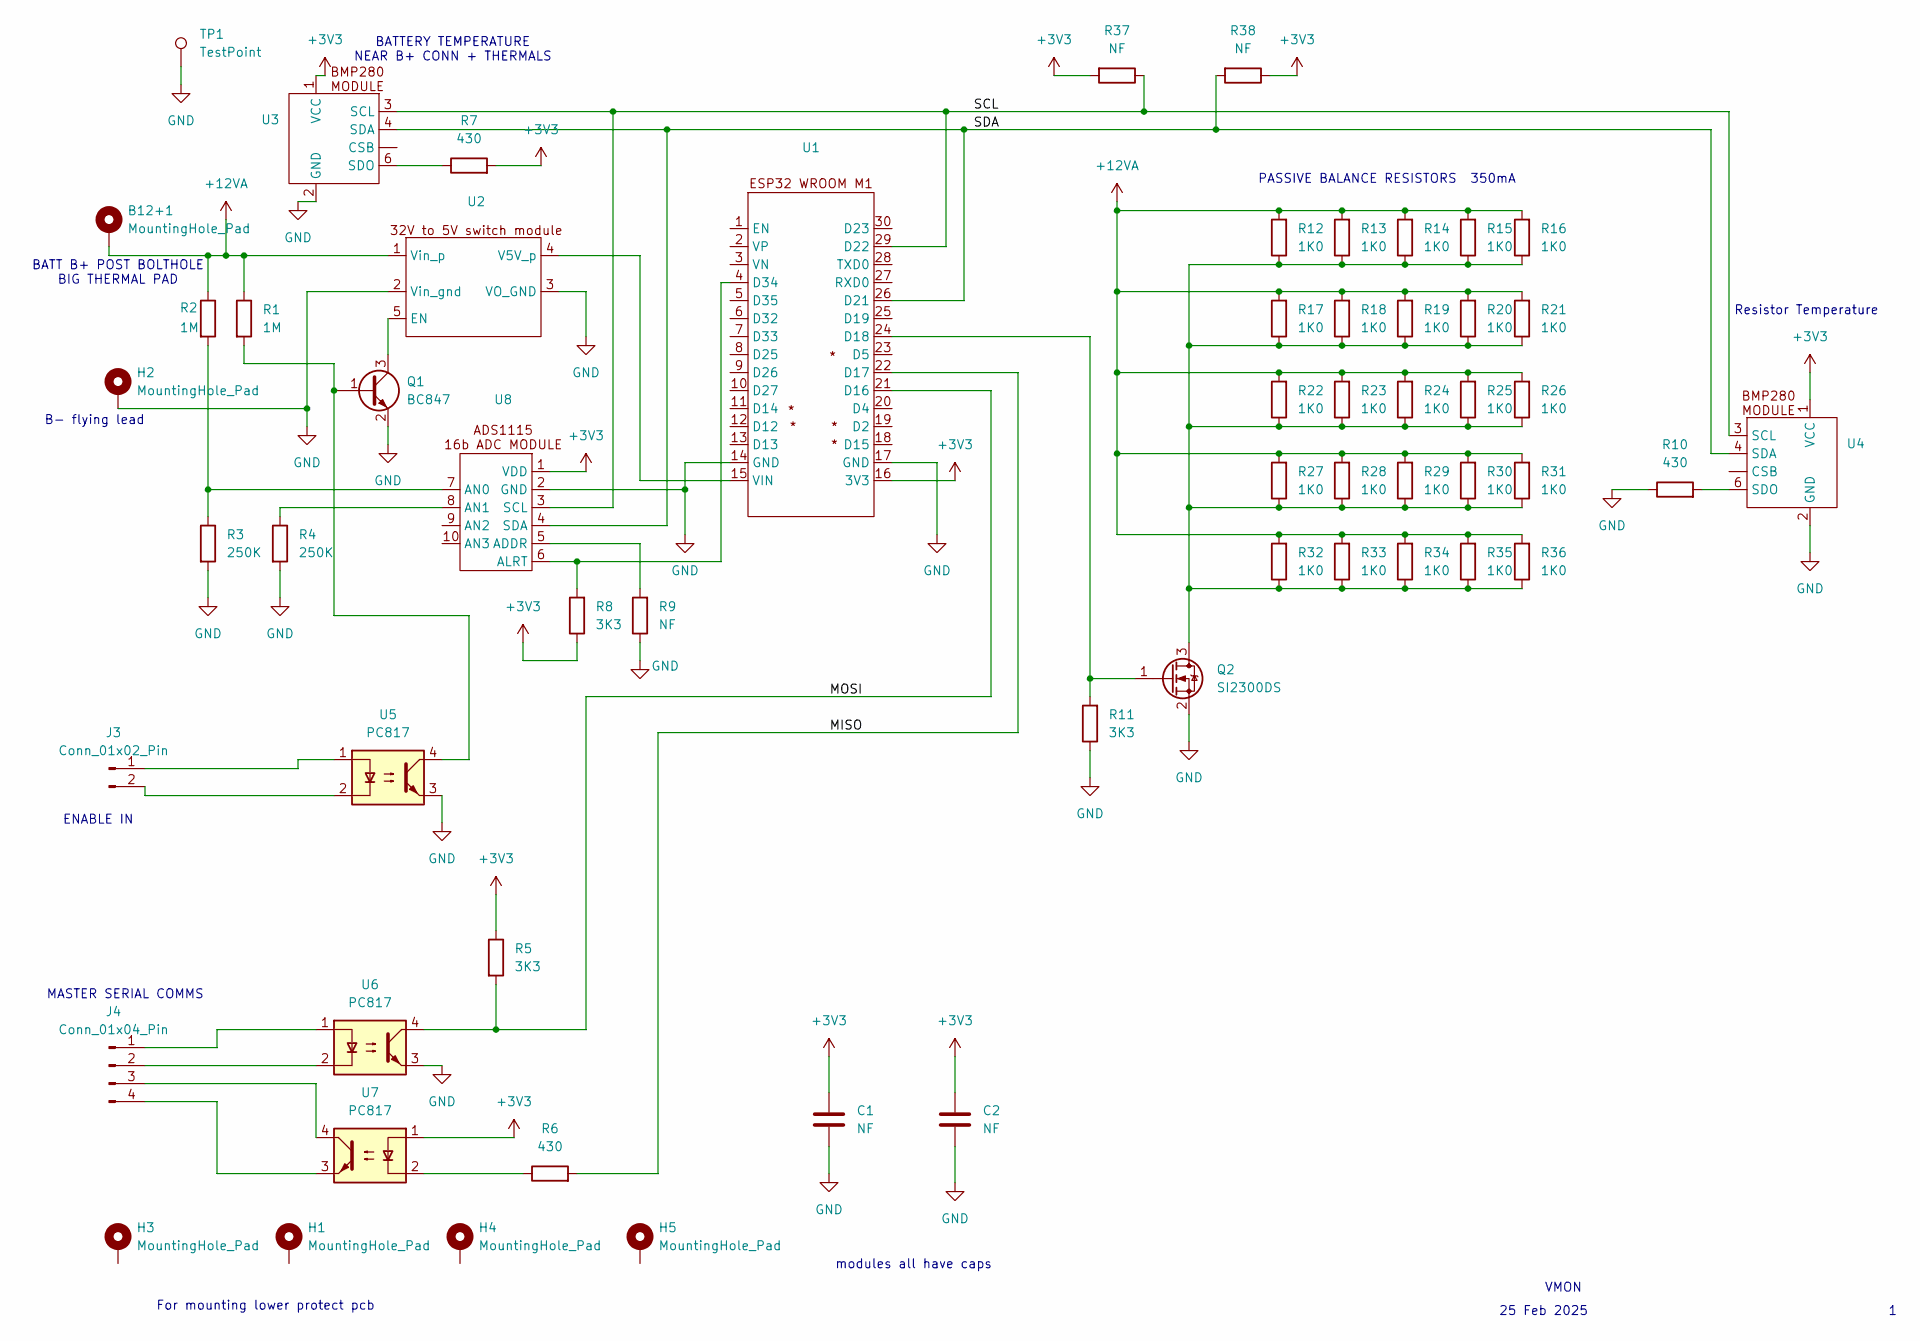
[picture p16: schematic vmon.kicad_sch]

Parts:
B12+1: MountingHole_Pad; MountingHole_8.4mm_M8_Pad_TopBottom
C1: NF; C_1210_3225Metric_Pad1.33x2.70mm_HandSolder
C2: NF; C_0603_1608Metric
H1, H3, H4, H5: MountingHole_Pad; MountingHole_3.2mm_M3_DIN965_Pad_TopBottom
H2: MountingHole_Pad; MountingHole_2.5mm_Pad_TopBottom
J3: Conn_01x02_Pin; PhoenixContact_MC_1,5_2-G-5.08_1x02_P5.08mm_Horizontal
J4: Conn_01x04_Pin; PhoenixContact_MC_1,5_4-G-5.08_1x04_P5.08mm_Horizontal
Q1: BC847; SOT-23
Q2: SI2300DS; SOT-23
R1, R2: 1M; R_0805_2012Metric_Pad1.20x1.40mm_HandSolder
R3, R4: 250K; R_0805_2012Metric_Pad1.20x1.40mm_HandSolder
R5, R8, R11: 3K3; R_0805_2012Metric_Pad1.20x1.40mm_HandSolder
R6, R7, R10: 430; R_0805_2012Metric_Pad1.20x1.40mm_HandSolder
R9, R37, R38: NF; R_0805_2012Metric_Pad1.20x1.40mm_HandSolder
R12, R13, R14, R15, R16, R17, R18, R19, R20, R21, R22, R23, R24, R25, R26, R27, R28, R29, R30, R31, R32, R33, R34, R35, R36: 1K0; R_2512_6332Metric_Pad1.40x3.35mm_HandSolder
TP1: TestPoint; Pin_D0.9mm_L10.0mm_W2.4mm_FlatFork
U1: ESP32_WROOM_M1
U2: switcher_en
U3, U4: R_Array_SIP6
U5, U6, U7: PC817; DIP-4_W7.62mm
U8: R_Array_SIP10

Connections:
+3V3: C1.1, C2.1, R5.1, R7.2, R8.1, R37.2, R38.1, U1.16 (3V3), U3.1 (VCC), U4.1 (VCC), U7.1, U8.1 (VDD)
+12VA: B12+1.1, R1.1, R2.1, R12.2, R13.2, R14.2, R15.2, R16.2, R17.2, R18.2, R19.2, R20.2, R21.2, R22.2, R23.2, R24.2, R25.2, R26.2, R27.2, R28.2, R29.2, R30.2, R31.2, R32.2, R33.2, R34.2, R35.2, R36.2, U2.1 (Vin_p)
/MISO: R6.2, U1.22 (D17)
/MOSI: R5.2, U1.21 (D16), U6.4
/SCL: R37.1, U1.29 (D22), U3.3 (SCL), U4.3 (SCL), U8.3 (SCL)
/SDA: R38.2, U1.26 (D21), U3.4 (SDA), U4.4 (SDA), U8.4 (SDA)
GND: C1.2, C2.2, H2.1, Q1.2 (E), Q2.2 (S), R3.2, R4.2, R9.1, R10.1, R11.1, TP1.1, U1.14 (GND), U1.17 (GND), U2.2 (Vin_gnd), U2.3 (VO_GND), U3.2 (GND), U4.2 (GND), U5.3, U6.3, U8.2 (GND)
unnamed: J3.1, U5.1
unnamed: J3.2, U5.2
unnamed: J4.1, U6.1
unnamed: J4.2, U6.2
unnamed: J4.3, U7.4
unnamed: J4.4, U7.3
unnamed: Q1.1 (B), R1.2, U5.4
unnamed: Q1.3 (C), U2.5 (EN)
unnamed: Q2.3 (D), R12.1, R13.1, R14.1, R15.1, R16.1, R17.1, R18.1, R19.1, R20.1, R21.1, R22.1, R23.1, R24.1, R25.1, R26.1, R27.1, R28.1, R29.1, R30.1, R31.1, R32.1, R33.1, R34.1, R35.1, R36.1
unnamed: Q2.1 (G), R11.2, U1.24 (D18)
unnamed: R6.1, U7.2
unnamed: R8.2, U1.4 (D34), U8.6 (ALRT)
unnamed: U1.15 (VIN), U2.4 (V5V_p)
unnamed: R7.1, U3.6 (SDO)
unnamed: R10.2, U4.6 (SDO)
unnamed: R9.2, U8.5 (ADDR)
unnamed: R2.2, R3.1, U8.7 (AN0)
unnamed: R4.1, U8.8 (AN1)

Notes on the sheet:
VMON
25 Feb 2025
BATTERY TEMPERATURE NEAR B+ CONN + THERMALS
For mounting lower protect pcb
B- flying lead
MASTER SERIAL COMMS
PASSIVE BALANCE RESISTORS 350mA
ENABLE IN
BATT B+ POST BOLTHOLE BIG THERMAL PAD
modules all have caps
Resistor Temperature

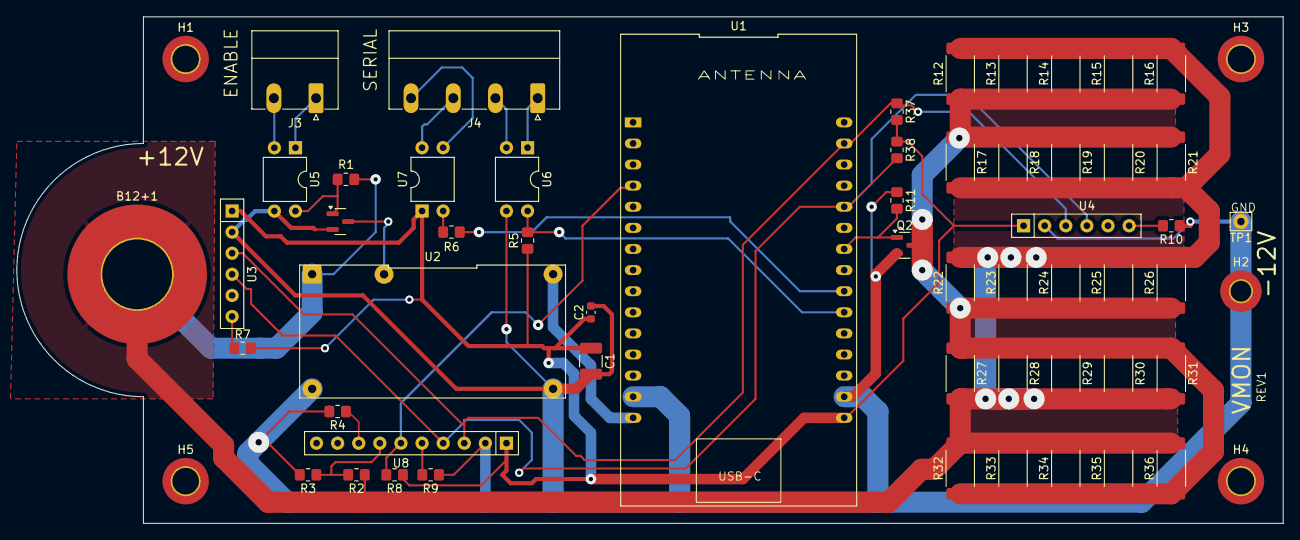
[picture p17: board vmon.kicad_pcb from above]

Board: 2 copper layers, 152.4 x 61.0 mm, 59 parts (0 on the bottom side), 25 nets.

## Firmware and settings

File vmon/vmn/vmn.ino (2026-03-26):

//    -*- Mode: c++     -*-
// emacs automagically updates the timestamp field on save
// my $ver =  'vmn   Time-stamp: "2026-03-26 18:00:52 john"';

// this is the app to run per battery vmon for the Ryobi mower.
// called vmn as vmon was taken for the pcb
// use tools -> board ->  ESP32 Dev module 

/*
  A vmon is per 12V LFP battery, and  runs off that battery.
  It physically bolts to the battery terminals.
  Its 12v to 5v switcher is enabled (by mco) (optically isolated) to minimize off state power consumption.
  It chats to mco  via wifi.  This is the esp_now() branch.

  Vmon contains a calibrated 16 bit ADC to monitor the battery voltage.
  Vmon contains a passive balance circuit (aka a load resistor) to allow charge to be removed
  from the battery under test.   It's 25 1K resistors in parallel,
  It is expected balancing will happen at about 3.45V/cell, or 13.8V for the 4 cell 12v battery. So thats 345mA
  Its up to mco to turn that balance resistor on and off, noting vmon will turn the resistor off if it gets too hot.
  mco has vision across all batteries, its vmon's job to balance the batteries. Probably only on charge, at cv operation near top-off.

  Vmon can monitor battery and resistor temperature. Battery temperatures ghet reported. resistor temperature is for self protection.

*/


#include <Preferences.h>  // the NV memory interface
#include <Wire.h>
#include <Adafruit_Sensor.h>
#include <Adafruit_BMP280.h>
#include "ESP32Time.h"   // must be V2.x or newer. V1.04 takes 5s to return a time string. breaks logging 
#include<ADS1115_WE.h>   // adc converter
#include <stdio.h>
#include <esp_now.h>
#include <WiFi.h>
#include <esp_wifi.h>
#define DEBUG

// for preferences
#define RW_MODE false
#define RO_MODE true


// serial0 is used for debug and for programming NVM
const uint8_t longest_record = 24;  //   worst is display comand WD1=12345678901234567890
const uint8_t record_size = longest_record + 2;    //  char char = nnnnn \n
char serial_buf[record_size];
uint8_t serial_buf_pointer;

const  uint16_t msgbuflen= 128;  // for serial responses
char return_buf[msgbuflen]; 

const char * version = "VMON espnow 26 Mar 2026 Reva";

Preferences vmonPrefs;  // NVM structure
// these will be initialized from the NV memory

uint8_t baseMac[6];         // my own mac address
uint8_t mco_mac[6];
uint8_t cmt_mac[6];

int     balance_on_temp;
int     balance_off_temp;
float   adc0;
float   adcgain;
uint8_t board_address;
int     s2baud;       // serial 2 baud rate
bool nap = false;
int32_t  nap_us;      // how long to nap for, in uS


/* IOs  definitions */
const uint8_t balance_en_pin  = 18;    // enable balance current dumper
const uint8_t alrt_pin  = 34;          // alert from adc
const uint8_t sda_pin   = 21;          // 
const uint8_t scl_pin   = 22;          //
const uint8_t rxd2_pin  = 16;          //
const uint8_t txd2_pin  = 17;          //

// I2C addresses 
const uint8_t battery_temperature_addr = 0x77;
const uint8_t resistor_temperature_addr = 0x76;
const uint8_t adc_addr = 0x48;

Adafruit_BMP280 tsenseB;    // I2C connected bmp280 temperature and pressure sensor. Used for Battery temp.
Adafruit_BMP280 tsenseR;    // I2C connected bmp280 temperature and pressure sensor. Used for Resistor temp.
ADS1115_WE adc = ADS1115_WE(adc_addr); // I2C connected ads1115 16b adcb  Used for battery voltage.

int     battery_temperature;     // current value of heatsink temperature for the mower switch.
int     resistor_temperature;    // current value of heatsink temperature for the mower switch.
bool    balance=false;           // true if mco has told me to balance.
float   voltage = 0.0;           // current battery voltage
bool    cal_we  = false;         // this is a write enable for cal from the wifi interface.
int16_t we_poll_cd =0;           // this poll counter decrements if positive every voltage read.
                                 // when 0, resets cal_we AND allows napping on polls to restart. 

ESP32Time rtc;
unsigned long last_temp_update_time;   // time last temperature was polled in seconds. 2 sensors alternate
const unsigned long temp_update_period = 5; // seconds.
bool doing_resistor_temp = true;

//unsigned long last_voltage_time;         // time last power supply voltage was touched
// const unsigned long voltage_update_period = 1;  // seconds.

// unsigned long last_vmon_time;         // time last power supply voltage and current was polled at



// create the wifi message struct

typedef struct struct_message {
  char message[msgbuflen];
} struct_message;

struct_message outgoing_data;
struct_message incoming_data;

esp_now_peer_info_t peerInfo;

// NB the following 2 callbacks are modified to match espnow libraries version 3 as per what I did for mco 1 Mar 2026.
// Tested to compile, but not programmed to device and tested in anger yet.   mco has been tested to balance as desired.

// wifi callback when data is sent
void OnDataSent(const wifi_tx_info_t *mac, esp_now_send_status_t status)
{
  if (we_poll_cd > 0)
    we_poll_cd--;           // poll counter used to inhibit napping under current testing and voltage cal.
  
  if (we_poll_cd == 0)
    {
      cal_we = false;
      if (nap)
	{ // nap here, as its called after the poll response has completed.
	  esp_wifi_stop();
	  esp_err_t result = esp_sleep_enable_timer_wakeup(nap_us);
	  esp_light_sleep_start();     // Enter light sleep
	  esp_wifi_start();
	}
    }
}


// callback function that will be executed when data is received
void OnDataRecv(const esp_now_recv_info_t *esp_now_info, uint8_t *incomingData, int len) {
  memcpy(&incoming_data.message, incomingData, sizeof(incoming_data));
  uint8_t *mac=esp_now_info->src_addr;

  // Serial.print("received ");
  // Serial.print(len);
  // Serial.print(" bytes from ");  
  // Serial.printf("%02x%02x%02x%02x%02x%02x\n", mac[12], mac[13], mac[14], mac[15], mac[16], mac[17]) ;
  /* I suspect the mac' field here is the 24 byte mac header structure espressif uses
     fields 12 to 17 seem to be the source MAC. rest isn't obvious */
  
  // from mco? 
  if ((mac[0] == mco_mac[0]) && (mac[1] == mco_mac[1]) && (mac[2] == mco_mac[2]) &&
      (mac[3] == mco_mac[3]) && (mac[4] == mco_mac[4]) && (mac[5] == mco_mac[5]))
    {
      parse_wifi_buf(incoming_data.message, outgoing_data.message, sizeof(outgoing_data.message));
      esp_now_send(mco_mac, (uint8_t *) &outgoing_data, sizeof(outgoing_data));
    }
}


void setup (void) {
  Wire.begin();  
  Serial.begin(115200);
  Serial.println(version);

  // reinit_NVM();  sometimes you have to reinit to get it to start, when stuff changes just so!
  
  
  /* init IOs */
  pinMode(balance_en_pin, OUTPUT);
  digitalWrite(balance_en_pin, 0);
  pinMode(alrt_pin, INPUT_PULLUP);

   // start temperature sensors
   if (!tsenseB.begin(battery_temperature_addr))
     {  
       Serial.print("Could not find a valid battery BMP280 sensor at address 0x");  
       Serial.println(battery_temperature_addr, HEX);  
     }
   battery_temperature = (int)  tsenseB.readTemperature();

   if (!tsenseR.begin(resistor_temperature_addr))
     {  
       Serial.print("Could not find a valid resistor BMP280 sensor at address 0x");  
       Serial.println(resistor_temperature_addr, HEX);  
     }
   resistor_temperature = (int)  tsenseR.readTemperature();
   
   // init adc
     if(!adc.init()){
       Serial.println("ADS1115 not connected!");
     }
     adc.setVoltageRange_mV(ADS1115_RANGE_4096);  // 4.096V input range.
                                                  // input attenuator about 0.2  0.2 * 15V max = 3V
     adc.setCompareChannels(ADS1115_COMP_0_1);    // measure between 0 and 1.
     adc.setConvRate(ADS1115_8_SPS);              // 8 samples per sec, slowest.
     adc.setAlertPinMode(ADS1115_DISABLE_ALERT);  // not using voltage range checks
     adc.setMeasureMode(ADS1115_CONTINUOUS);      // initiate measurements
   
   // check NVM looks defined  
   vmonPrefs.begin("vmonPrefs", RO_MODE);     // Open our namespace (or create it if it doesn't exist)
   bool tpInit = vmonPrefs.isKey("nvsInit"); // Test for the existence of the "already initialized" key.
   vmonPrefs.end();                          // close the namespace in RO mode
   if (tpInit == false) 
     reinit_NVM();                          // reinitialize the nvm structure if magick key was missing 
   
   // load local variables from NVM
   load_operational_params();                // load all variables from NVM

   // init some general variables and IOs 
   serial_buf_pointer = 0;
   cal_we = false;
   we_poll_cd = 0;
   
   // init esp_now wifi 
   WiFi.mode(WIFI_STA);

   esp_err_t ret = esp_wifi_get_mac(WIFI_IF_STA, baseMac);
   Serial.printf("ESP32 MAC Address: %02x%02x%02x%02x%02x%02x\n",
		 baseMac[0],baseMac[1],baseMac[2],baseMac[3],baseMac[4],baseMac[5]);

   Serial.println("init espnow");
   if (esp_now_init() != ESP_OK) {
     Serial.println("Error initializing ESP-NOW");
     return;
   }

   // Once ESPNow is successfully Inited, we will register for Send CB to
   // get the status of Trasnmitted packet
   esp_now_register_send_cb(OnDataSent);
    
   // Once ESPNow is successfully Inited, we will register for recv CB to
   // get recv packer info
   esp_now_register_recv_cb(esp_now_recv_cb_t(OnDataRecv));

    Serial.println("register macs");
    // Register peer mco
    memcpy(peerInfo.peer_addr, mco_mac, 6);
    peerInfo.channel = 0;  
    peerInfo.encrypt = false;
    
    if (esp_now_add_peer(&peerInfo) != ESP_OK){
      Serial.println("Failed to add peer");
    }
    // Register peer cmt
    memcpy(peerInfo.peer_addr, cmt_mac, 6);
    if (esp_now_add_peer(&peerInfo) != ESP_OK){
      Serial.println("Failed to add peer");
    }
   Serial.println("done setup");
}

   

void loop (void)
{
  // service serial character if any available.
  do_serial_if_ready();

  // update temperature and monitor balance state if its due 
  if (rtc.getEpoch() > (last_temp_update_time + temp_update_period))
    {
      if (doing_resistor_temp)
	{
	  resistor_temperature = (int)  tsenseR.readTemperature();
	  doing_resistor_temp = false;
	  if (balance)
	    {
	      if (digitalRead(balance_en_pin) && (resistor_temperature >= balance_off_temp))
		digitalWrite(balance_en_pin, 0);
	      else if (!digitalRead(balance_en_pin) && (resistor_temperature <= balance_on_temp))
		digitalWrite(balance_en_pin, 1);
	    }
	}
      else
	{
	  battery_temperature = (int)  tsenseB.readTemperature();
	  doing_resistor_temp = true;
	}
      last_temp_update_time = rtc.getEpoch();
    }
}

float get_voltage ()
{
  float volt;
  volt = adcgain * (adc.getResult_V() + adc0);
  return volt;
}
  
const uint8_t default_mac[]     = { 0xff, 0xff, 0xff, 0xff, 0xff, 0xff };
const uint8_t default_mco_mac[] = { 0x5c, 0x01, 0x3b, 0x6c, 0x6a, 0x44 };
const uint8_t default_cmt_mac[] = { 0x5c, 0x01, 0x3b, 0x6c, 0x99, 0x38 };

void reinit_NVM (void)
{
  Serial.println("Initializing NVM");
  
  // If tpInit is 'false', the key "nvsInit" does not yet exist therefore this
  //  must be our first-time run. We need to set up our Preferences namespace keys. So...
  vmonPrefs.begin("vmonPrefs", RW_MODE);       //  open it in RW mode.
  
  // The .begin() method created the "vmnPrefs" namespace and since this is our
  //  first-time run we will create
  //  our keys and store the initial "factory default" values.

  vmonPrefs.putInt("s2baud", 9600);          // baud rate serial 2 DPM8624
  vmonPrefs.putInt("bal_on_temp", 50);       // turn balance on again when temp gets this low
  vmonPrefs.putInt("bal_off_temp", 70);      // turn balance off if resistors getthis hot
  vmonPrefs.putFloat("adcgain", 5.3);        // approx adc gain term
  vmonPrefs.putFloat("adc0", 0.0);           // adc 0 offset term
  vmonPrefs.putUChar("address", '0');        // board address
  vmonPrefs.putBytes("cmtmac", default_cmt_mac, 6);  // mac address of tester
  vmonPrefs.putBytes("mcomac", default_mco_mac, 6);  // mac address of mower comms controller 
  vmonPrefs.putBool("nap", true);             // Nap After Poll  after wifi poll?"
  vmonPrefs.putLong("nap_us", 280000);         // nap time in us. about 3/4  of the poll period
  vmonPrefs.putBool("nvsInit", true);         // Create the "already initialized"
  //  key and store a value.
  // The "factory defaults" are created and stored so...
  vmonPrefs.end();                               // Close the namespace in RW mode and...
}


void load_operational_params(void)
{

  vmonPrefs.begin("vmonPrefs", RO_MODE);       // Open our namespace (or create it
                                             //  if it doesn't exist) in RO mode.
   // Retrieve the operational parameters from the namespace
   //  and save them into their run-time variables.
  s2baud           = vmonPrefs.getInt("s2baud");          // baud rate serial 2 DPM8624
  balance_on_temp  = vmonPrefs.getInt("bal_on_temp");     // turn balance on again when temp gets this low
  balance_off_temp = vmonPrefs.getInt("bal_off_temp");    // turn balance off if resistors getthis hot
  adcgain          = vmonPrefs.getFloat("adcgain");       // adc gain term
  adc0             = vmonPrefs.getFloat("adc0");          // adc 0 offset term
  board_address    = vmonPrefs.getUChar("address");         // board address
  vmonPrefs.getBytes("mcomac", mco_mac, 6);             // load mco comms controller mac
  vmonPrefs.getBytes("cmtmac", cmt_mac, 6);             // load cmt tester mac
  nap = vmonPrefs.getBool("nap");                       // Nap After Poll  after wifi poll?"
  nap_us = vmonPrefs.getLong("nap_us");                 // nap time in uS
  
   // All done. Last run state (or the factory default) is now restored.
   vmonPrefs.end();                                      // Close our preferences namespace.
}

void parse_buf (char * in_buf, char * out_buf, int out_buf_len)
{
  // Z eraZe NV memory
  // Rf Read and print Field,
  //    where Field could be   lower case comamnds tend to be immediate things, UPPER case is NVM
  //         A board address 1..4
  //         B baud rate on S2
  //         G adc gain
  //         H high balance temperature 
  //         L low balance temperature
  //         N nap and Nap_us
  //         M Mac addresses I know about
  //         O adc offset
  //         V version
  //         b  balance requested setting
  //         c  balance actual setting
  //         v latest voltage
  //         r  resistor latest temperature
  //         s  battery latest temperature
  // W%c[%c]=value,
  //    where Field could be:     lower case comamnds tend to be immediate things, UPPER case is NVM
  //         A=%d board address 1..4
  //         B=%d baud rate on S2
  //         G=%f adc gain
  //         H=%d highbalance temperature 
  //         L=%d low balance temperature  
  //         M[CO]=%f Macs for mcO or Cmt
  //         NE=b   nap after poll, a boolean enable
  //         NT=d   nap time in uS. default 280,000us
  //         O=%f adc offset
  //         b=%b balance               

  uint8_t read_pointer = 0;
  uint8_t  cmd;
  uint8_t  field;
  uint8_t  field2;
  int      value;
  float    fvalue;
  int match ;
  uint8_t  mvalue[6]; // mac address
  cmd = in_buf[read_pointer++];
  out_buf[0]=0;
  
  switch (cmd) {
  case 'Z':
    reinit_NVM();
    load_operational_params();
    break;

  case 'R':
    field = in_buf[read_pointer++];
    switch (field)
      {
      case 'A':
	snprintf(out_buf, out_buf_len, "address=%c\n", board_address);
	break;

      case 'B':
	snprintf(out_buf, out_buf_len, "s2baud=%d\n", s2baud);
	break;

      case 'G':
	snprintf(out_buf, out_buf_len, "adc_gain=%f\n", adcgain);
	break;

      case 'H':
	snprintf(out_buf, out_buf_len, "balance_off=%dC\n",balance_off_temp );
	break;

      case 'L':
	snprintf(out_buf, out_buf_len, "balance_on=%dC\n", balance_on_temp);
	break;
      case 'M':

	Serial.printf("VMON_MAC=%02x%02x%02x%02x%02x%02x  MCO=%02x%02x%02x%02x%02x%02x CMT=%02x%02x%02x%02x%02x%02x\n",
		      baseMac[0],baseMac[1],baseMac[2],baseMac[3],baseMac[4],baseMac[5],
		      mco_mac[0],mco_mac[1],mco_mac[2],mco_mac[3],mco_mac[4],mco_mac[5],
		      cmt_mac[0],cmt_mac[1],cmt_mac[2],cmt_mac[3],cmt_mac[4],cmt_mac[5]);
	break;

      case 'N':
	snprintf(out_buf, out_buf_len, "nap_en=%1d nap_time=%d we_poll_cd=%d\n", nap, nap_us, we_poll_cd);
	break;

      case 'O':
	snprintf(out_buf, out_buf_len, "adc_offset=%f\n", adc0);
	break;

      case 'V':
	snprintf(out_buf, out_buf_len, "%s\n", version);
	break;

      case 'b':
	snprintf(out_buf, out_buf_len, "balance_req=%d\n", balance);
	break;

      case 'c':
	snprintf(out_buf, out_buf_len, "balance_pin=%d\n", digitalRead(balance_en_pin));
	break;

      case 'v':
	  snprintf(out_buf, out_buf_len, "voltage=%fV\n", get_voltage());
	break;

      case 'r': // had to go UTF8 to get the degree symbol in serial monitor
	  snprintf(out_buf, out_buf_len, "resistor_temp=%d%c%cC\n", resistor_temperature, char(0xC2), char(0xB0));
	break;

      case 's':
	snprintf(out_buf, out_buf_len, "battery_temp=%d%c%cC\n", battery_temperature, char(0xc2),char(0xb0));
	break;
      }
      break;
    

  case 'W':
    {
      // first case, WA=3     decimal integer up to ~5 sig figures
      match =  sscanf(in_buf, "%c%c=%d", &cmd, &field, &value);
      //  if (match == 3)
      // Serial.printf("bal request %d\n", value);
      switch (field) {
      case 'b' :   // balance
	if (value == 0)
	  {
	    balance = false;
	    digitalWrite(balance_en_pin, LOW);
	  }
	else
	  {
	    balance = true;
	    digitalWrite(balance_en_pin, HIGH);
	  }
	snprintf(out_buf, out_buf_len, "ok\n");
	break;
	
      case 'A':
	vmonPrefs.begin("vmonPrefs", RW_MODE);         // Open our namespace for write
	vmonPrefs.putUChar("address", in_buf[3]);               
	vmonPrefs.end();                              // Close the namespace
	load_operational_params();
	break;
	
      case 'B':
	vmonPrefs.begin("vmonPrefs", RW_MODE);         // Open our namespace for write
	vmonPrefs.putInt("s2baud", value);               
	vmonPrefs.end();                              // Close the namespace
	load_operational_params();
	break;
	
      case 'H':
	vmonPrefs.begin("vmonPrefs", RW_MODE);         // Open our namespace for write
	vmonPrefs.putInt("bal_off_temp", value);               
	vmonPrefs.end();                              // Close the namespace
	load_operational_params();
	break;
	
      case 'L':
	vmonPrefs.begin("vmonPrefs", RW_MODE);         // Open our namespace for write
	vmonPrefs.putInt("bal_on_temp", value);               
	vmonPrefs.end();                              // Close the namespace
	load_operational_params();
	break;
	
      case 'G':
	match =  sscanf(in_buf, "%c%c=%f", &cmd, &field, &fvalue);
	vmonPrefs.begin("vmonPrefs", RW_MODE);         // Open our namespace for write
	vmonPrefs.putFloat("adcgain", fvalue);               
	vmonPrefs.end();                              // Close the namespace
	load_operational_params();
	break;
	
      case 'M':  // WMP=MACADDRESS for the guy to respond to
	match =  sscanf(in_buf, "%c%c%c=%2x%2x%2x%2x%2x%2x", &cmd, &field,&field2,
			&mvalue[0],&mvalue[1],&mvalue[2],&mvalue[3],&mvalue[4],&mvalue[5]);
	
	vmonPrefs.begin("vmonPrefs", RW_MODE);         // Open our namespace for write
	if (field2 == 'O') 
	  vmonPrefs.putBytes("mcomac", mvalue, 6);
	else if (field2 == 'C') 
	  vmonPrefs.putBytes("cmtmac", mvalue, 6);
	vmonPrefs.end();                              // Close the namespace
	load_operational_params();
	break;
	
      case 'N':
	match =  sscanf(in_buf, "%c%c%c=%d", &cmd, &field, &field2, &value);
	vmonPrefs.begin("vmonPrefs", RW_MODE);         // Open our namespace for write
	if (field2 == 'E')
	  vmonPrefs.putBool("nap", value);
	else if (field2 == 'T')
	  vmonPrefs.putLong("nap_us", value);
	vmonPrefs.end();                              // Close the namespace
	load_operational_params();
	break;

      case 'O':
	match =  sscanf(in_buf, "%c%c=%f", &cmd, &field, &fvalue);
	vmonPrefs.begin("vmonPrefs", RW_MODE);         // Open our namespace for write
	vmonPrefs.putFloat("adc0", fvalue);               
	vmonPrefs.end();                              // Close the namespace
	load_operational_params();
	break;
	
      }      
      break;
      // end of 'W'
    }
  }
}

// S1 msg  gets parsed
 
void do_serial_if_ready (void)
{
  int serial_byte;
  if (Serial.available())
    {
      serial_byte = Serial.read();
      if ((serial_byte != '\n') && (serial_buf_pointer < longest_record))
	{
	  serial_buf[serial_buf_pointer] = serial_byte;  // write char to buffer if space is available
	  serial_buf_pointer++;
	}    
      if (serial_byte == '\n')
	{
	  serial_buf[serial_buf_pointer] = (uint8_t) 0;  // write string terminator to buffer
	  if (serial_buf_pointer >= 1)                  // at least a command letter
	    {
	      parse_buf(serial_buf, return_buf, 127);  // parse the buffer if at least one char in it.
	      Serial.print(return_buf);
	    }
	  serial_buf_pointer = 0;
	}
    }
}
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

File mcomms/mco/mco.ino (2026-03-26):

//    -*- Mode: c++     -*-
// emacs automagically updates the timestamp field on save
// my $ver =  'mco  Time-stamp: "2026-03-26 17:40:10 john"';

// this is the app to run the mower comms controller for the Ryobi mower.
// use tools -> board ->  ESP32 Dev module 

/* mco is responsible for talking to the 4 vmons.
   And, directly,  psu.  to adjust current and voltage settings.
   It has to report all relevant loggable info to mcc.
   It has to get the info from vmons. It runs all this.

   Locally, mco WAS SUPPOSED to have access to the current into/out of the batteries via current shunt and adc
   but my design was broken, the adc doesn't do bipolar inputs which the design needed.
   Now there is an imon board, with the same type adc on an isolated supply rail board, the shunt is biassed
   to mid rail. Data gets to mco via wifi, just like everything else.
   
   MCO integrates current to get SOC.
   It zeros SOC on empty, one day adjusting the battery capacity measure when that happens.
   It 100%s SOC on full, one day adjusting the battery capacity measure when that happens.
   It beeps  when battery SOC at ~10% && not_charging
   it records SOC in local fram.  3 copies currently.

   It controls power supply settings on charge to implement a main charge CC phase transitioning to CV as
   current drops below the preset max current. When current falls enough, switches state to a higher
   voltage, lower current setting for a topoff phase, where the balancers can kick in and make a significant
   effect.
   When current is low enough, or individual battery voltage high enough, it all stops.
*/

#include "mco_data.h"


// wifi callback when data is sent (nb type change of the tx_struct for newer esp library)
void OnDataSent(const wifi_tx_info_t *mac_addr, esp_now_send_status_t status)
{
}


// callback function that will be executed when data is received
// noting that this is called from a high priority task, so should not do anything slow.
void OnDataRecv(const esp_now_recv_info_t *esp_now_info, uint8_t *incomingData, int len) {
  memcpy(&incoming_data, incomingData, sizeof(incoming_data));
  uint8_t *mac=esp_now_info->src_addr;
  // Serial.print("received ");
  // Serial.print(len);
  // Serial.print(" bytes from ");  
  // Serial.printf("%02x%02x%02x%02x%02x%02x\n", mac[12], mac[13], mac[14], mac[15], mac[16], mac[17]) ;

  // from psu?  Record polled readings. more differences at end of mac string
  if ((mac[5] == psu_mac[5]) && (mac[4] == psu_mac[4]) && (mac[3] == psu_mac[3]) &&
      (mac[2] == psu_mac[2]) && (mac[1] == psu_mac[1]) && (mac[0] == psu_mac[0]))
    parse_psu_wifi_buf(incoming_data.message);
  // from imon?  Record unpolled readings
  else if ((mac[0] == imon.mac[0]) && (mac[1] == imon.mac[1]) && (mac[2] == imon.mac[2]) &&
      (mac[3] == imon.mac[3]) && (mac[4] == imon.mac[4]) && (mac[5] == imon.mac[5]))
    parse_imon_wifi_buf(incoming_data.message);
  // from a vmon?  Record polled readings
  else {
    uint8_t i;
    for (i=0; i< vmons; i++)
      {
	if ((mac[5] == vmon[i].mac[5]) && (mac[4] == vmon[i].mac[4]) && (mac[3] == vmon[i].mac[3]) &&
	    (mac[2] == vmon[i].mac[2]) && (mac[1] == vmon[i].mac[1]) && (mac[0] == vmon[i].mac[0]))
	  parse_vmon_wifi_buf(incoming_data.message, i);
      }
  }
}
void setup (void) {
  Wire.begin();   //   Including Wire.begin seems to break FRAM ???
  Serial.begin(115200);
  Serial.println(version);
  
  // interestingly, while rx=16 txd=17 is supposedly the default pin allocation,  Serial2 doesn't
  // work without explicitly filling in the pin numbers here
  //Serial2.begin(9600, SERIAL_8N1, 16, 17);  

  //init vmon structure
  int i;
  int j;
  
  for (i=0;i<vmons;i++)
    {
      vmon[i].volt=0.0;
      vmon[i].battemp=0;
      vmon[i].restemp=0;
      vmon[i].mostrecent=0;
      vmon[i].received=0;
      vmon[i].sent=0;
      vmon[i].balance=0;
      vmon[i].protocol_err=0;
      vmon[i].act_balance=255;
      vmon[i].gain = -1;
      vmon[i].offset = -1;
    }
  vmon_struct_loaded = false;

  // init imon struct
      imon.current=0.0;
      imon.mostrecent=0;
      imon.received=0;
      imon.protocol_err=0;
  
  
  //init vmon command q
  for (i=0;i<cmdqlen;i++)
    {
      // vq[i].cmd=(char) 0;
      vq[i].cmd_avail=0;
      vq[i].qclaimed=0;
    }

  // init the vmon polling management struct
  for (i=0; i<vmon_ii_max; i++)    // set which vmon to poll     ie the vmon poll address
	vpoll[i].addr = i & 0x03;  // poll vmons in order 0,1,2,3,0,1,2,3 etc
  for (i=0;i<vmons;i++)              
    {                                 // set what to poll for each of the 4 vmons
      vpoll[i].letter         = 'v';  // first do a read voltage  for each vmon
      vpoll[i+  vmons].letter = 's';  // then do a read battery temp for each vmon
      vpoll[i+2*vmons].letter = 'r';  // then do a read resistor temp for each vmon
      vpoll[i+3*vmons].letter = 'v';  // then do another read voltage poll for each vmon
      vpoll[i+4*vmons].letter = 'B';  // then do a write balance  for each vmon
      vpoll[i+5*vmons].letter = 'b';  // then do a read actual balance state poll for each vmon, monitor for temp effects
    }

  // init charger structure
  charger.voltage = 0.0;
  charger.current = 0.0;
  charger.enable = 0;
  charger.mostrecent = 0;
  charger.sent = 0;
  charger.received = 0;
  State = Charger_not_init;
    
  
  Serial.println("init NVM");
  // initialize NVM  
   mcoPrefs.begin("mcoPrefs", RO_MODE);     // Open our namespace (or create it if it doesn't exist)
   bool tpInit = mcoPrefs.isKey("nvsInit"); // Test for the existence of the "already initialized" key.
   mcoPrefs.end();                          // close the namespace in RO mode
   if (tpInit == false) 
     reinit_NVM();                          // reinitialize the nvm structure if magik key was missing 
   
   // load local variables from NVM
   load_operational_params();                // load all variables from NVM

   // init IO
   pinMode(fram_wp_pin, OUTPUT);
   pinMode(buz_en_pin, OUTPUT);
   pinMode(alrt_pin, INPUT);
   pinMode(charger_connected_pin, INPUT);
   pinMode(soc_pps_pin, OUTPUT);

   digitalWrite(fram_wp_pin,  HIGH);
 
   // buzzer allocate
#ifdef DC_BEEPER
   digitalWrite(buz_en_pin, 0);
#else
   ledcAttach(buz_en_pin, freq_beep, beep_res);
   ledcWriteTone(buz_en_pin, 0);
#endif
   // soc allocate
   ledcAttach(soc_pps_pin, freq_soc_50, resolution);

   //   ledcWrite(buz_en_pin, 0);     // beeper off
   ledcWrite(soc_pps_pin, 128);  // set soc gauge to 50%
   

   // init some general variables and IOs 
   serial_buf_pointer = 0;
   last_current_update_time = rtc.getEpoch();
   last_display_update_time = rtc.getEpoch();
   last_charger_state_update_time = rtc.getEpoch();

   // at startup, confirm all 4 vmons are present.
   // play a beep code if not so.
   Serial.println("init FRAM");
   //   if (!fram.begin(0x50, fram_wp_pin))
   if (!fram.begin(0x50))
     {
       Serial.println("FRAM not connected!");
     }
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

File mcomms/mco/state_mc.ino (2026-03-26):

//    -*- Mode: c++     -*-
// emacs automagically updates the timestamp field on save
// my $ver =  'mco state machine  Time-stamp: "2026-03-26 18:32:32 john"';

// main functions for loop() in mco,  the state machine implementing the main runtime functionality


void update_charge_state_machine (void)
{
       
  // don't do much of this if I don't have a few readings from every vmon. Like when I'm bench testing a component.
  if (vmon_struct_loaded == false)
    if ((vmon[0].received > 20) && (vmon[1].received > 20) && (vmon[2].received > 20) && (vmon[3].received > 20))
      vmon_struct_loaded = true;


  // initialize the state structure when mowing
  if ( (State == Mowing) && (digitalRead(charger_connected_pin)==1))
    // hmmm, what about if I was mowing and now Im not.
    State = Charger_not_init;

  // process the state machine
  if (digitalRead(charger_connected_pin)==0)
    {
      State = Mowing;
      if (vmon_struct_loaded && 
	  ((vmon[0].volt < min_battery_voltage) ||(vmon[1].volt < min_battery_voltage) ||
	   (vmon[2].volt < min_battery_voltage) ||(vmon[3].volt < min_battery_voltage)))
	{ // a battery voltage is too low, set soc to 0% so beeping should start
	  soc  =  0;
	  write_SOC(0, soc );
	}
    }

  // items below here mean the charger is plugged in. It may not necessarily be either turned on on nor enabled.
  else if (State == Charger_not_init)
    { // as I don't know if the charger is actually on and listening, repeat this till  
      set_psu_e(0);  // should already be disabled.
      set_psu_v(initial_charge_voltage);
      set_psu_i(initial_charge_current);
      // don't leave this state till I'm sure the prior settings were correctly received by the charger
      if ((charger.set_v >= (initial_charge_voltage - charger_voltage_tol)) 
	  && (charger.set_v <= (initial_charge_voltage + charger_voltage_tol)) 
	  && (charger.set_i >= (initial_charge_current - charger_current_tol)) 
	  && (charger.set_i <= (initial_charge_current + charger_current_tol))) 
	State = Charger_init_CC;
    }
  
  else if (State == Charger_init_CC)
    {
      set_psu_e(1);
      if (imon.current > (1.1*transition_current)) // charger is now actually charging...)
	{
	  // checking the imon current inherantly checks the enable happened.
	  State = CC;
	}
    }


  //  as at 26 Feb 2026, I see this clause not executing because an unbalanced battery gets to max_battery_voltage before the transition current is reached.
  // I suspect another condition needs to exit state==CC when any cell gets somewhat close to max_cell_v  .  tcc perhaps should be comparable to balance current too. 

  else if ((State == CC) && ((charger.current < transition_current)
			     ||
			     ((vmon[0].volt > batt_balance_voltage) ||(vmon[1].volt > batt_balance_voltage) ||
			     (vmon[2].volt > batt_balance_voltage) ||(vmon[3].volt > batt_balance_voltage))))
    {
      set_psu_e(0);
      set_psu_v(topoff_charge_voltage);
      set_psu_i(topoff_charge_current);
      // don't leave this state till I'm sure the prior settings were correctly received by the charger
      if ((charger.set_v >= (topoff_charge_voltage - charger_voltage_tol)) 
	  && (charger.set_v <= (topoff_charge_voltage + charger_voltage_tol)) 
	  && (charger.set_i >= (topoff_charge_current - charger_current_tol)) 
	  && (charger.set_i <= (topoff_charge_current + charger_current_tol))) 
	State = Charger_init_CV;
    }


  else if ((State == Charger_init_CV))
    {
      set_psu_e(1);
      if (imon.current > (topoff_charge_current/2)) // charger is now actually charging...)
	{
	  // checking the imon current inherantly checks that the enable happened.
	  State = CV;
	}
    }
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

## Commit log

2025-02-14 added timeout, added hostname but that doesn't work with starlink router
    [relaybox.ino]
2025-02-15 seems to work for voltsdc and mv
2025-02-17 add a schematic for posterity
    [vichyctl.kicad_sch]
2025-02-18 add schematic too
    [relaybox.kicad_sch]
2025-02-28 drew 4 boards, asked pcbway to make some
    [mcharger_if-B_Cu.gbr, mcharger_if-B_Mask.gbr, mcharger_if-Edge_Cuts.gbr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]
2025-03-09 basic parser, temperature, nvm going
2025-03-09 got encoder running
2025-03-10 chased down a logging slownest bug in old ESP32Time library
    [mcc.ino]
2025-03-12 psu seems to work well with cmt now. calibration unconsidered
2025-03-14 initial write of mco. Required some changes to string formats from other boards. Still missing some core behaviour logic
    [mcc.ino, mco.ino, psu.ino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]
2025-03-15 tweaked vmon to run adc continuous, and read voltage on request not in the background. Tweaked mcc to performance instrument a serial poll
2025-03-17 got buzzer going. carsh on batt_capacity=0 hard to find
    [mco.ino]
2025-03-17 got buzzer and gauge going now, updatingnot just the first time. Buzzer is too quiet!
    [mco.ino]
2025-03-23 restructure cal a bit to allow mm resistor to cool and stabilize
    [mco.ino, vmn.ino]
2025-03-24 get remade imon up. implement napping for power reasons. Negate gain so + current is charge, increasing SOC
2025-03-31 wasn't updating charget.mostrecent. Added stat read for mco
2025-03-31 make current output to psu an int32_t. which is probably the default.
2025-04-01 merged in a couple of mco changes from laptop yesterday
2025-04-01 and fixed an obsolete header comment on mco
    [mco.ino]
2025-04-02 take current from imon preferably
2025-04-02 allow control of SM update period. Current set isn't working and SM affects debug.
2025-04-02 charger packet counts, fixed state mc poll time source
    [mco.ino]
2025-04-02 charger poll set and actual v, i
2025-04-02 move time resets to nearer the start, so repeating is closer desired period
    [mco.ino]
2025-04-02 implement a prog. timeout in psu to disable output on no wifi messages. Like when the mower is not powered up.
2025-04-06 initial attempt to prevent duplication of logging blocks. Untested
    [mcc.ino]
2025-04-07 tracked down mcc logging bug. Was doing a flush on close
    [mcc.ino]
2025-04-08 actually draw an imon schematic
    [imon.kicad_sch]
2025-04-08 add a top level schematic
    [mcharger_if.kicad_sch, mcomms.kicad_sch, mower_system_connect.kicad_sch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]
2025-04-08 realized the charger_connected mod to mco wasn't on the schematic
    [mcomms.kicad_sch]
2025-04-08 Kings battery web page now has more info on the internal BMS. Bumping the topoff voltage and beep threshold accordingly
2025-04-20 testing the state transition checks on charge after a mow, checked the current voltage not the set voltage. A bug
    [mco.ino, mco_data.h, state_mc.ino]
2025-04-20 sigh, stuck in state=2. ==2?
    [mco_data.h, state_mc.ino]
2025-04-23 rework beep to use floats on IO.
    [mcc_data.h, mco_data.h, nvm.ino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]
2026-03-01 change vichyctl to register hostname to dhcp. Change mco to also exit state 3 on batery reaching balance voltage
2026-03-01 modified psu, vmn, mcc, imon arduino files to compile against v3 espnow api. mco balanced last night on the mower with SM changes in the prior commit, and topping current set to 0.35A in the nvm. Tha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
2026-03-26 bracket typo
